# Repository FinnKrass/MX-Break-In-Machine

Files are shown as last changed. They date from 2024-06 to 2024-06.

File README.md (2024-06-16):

# MX Style Switch Break In Machine

Repository is still a work in progress!

A unique take on the switch break in machine intended to streamline the process and maximise outcomes. Useful for those who want to improve the sound and feeling of MX style keyboard switches that come scratchy/inconsistent from the factory.

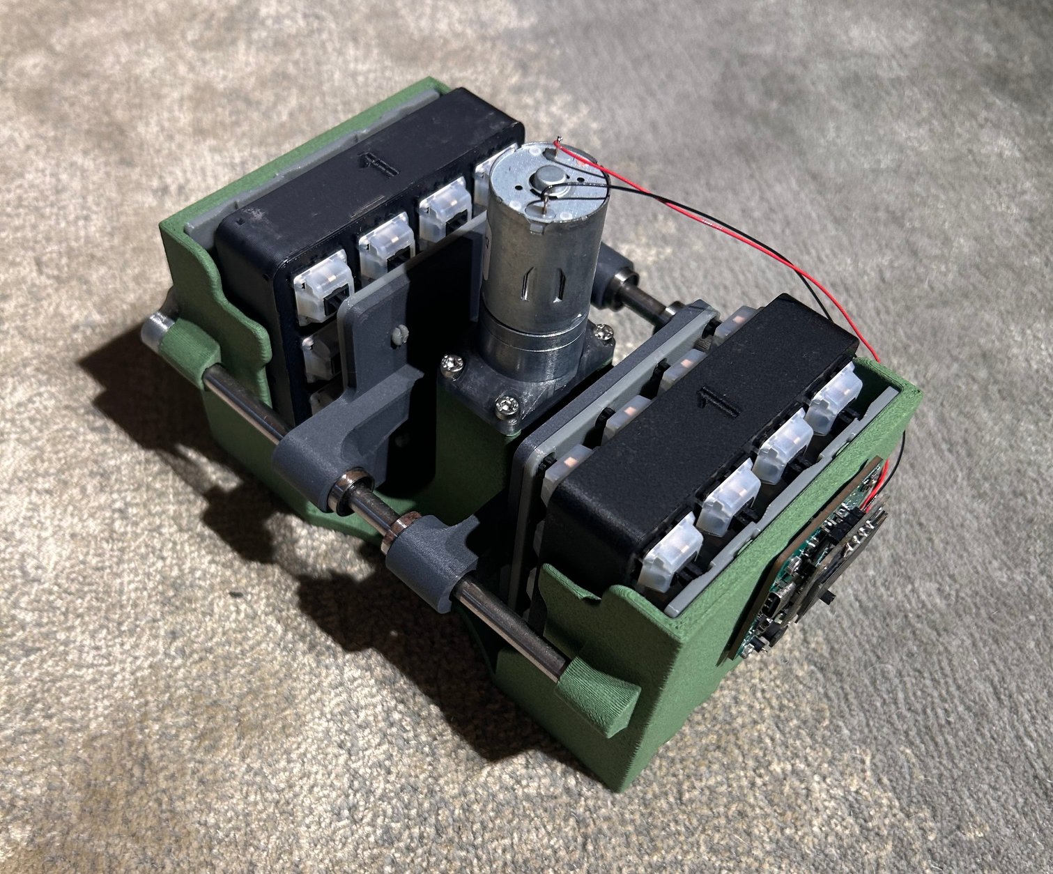
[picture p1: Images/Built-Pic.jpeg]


**Table of Contents:**

- [Main README](#mx-style-switch-break-in-machine)
  
  - [Background](#background)
  
  - [Features](#features)
  
  - [To Do](#to-do)
  
  - [References & Thanks](#references--thanks)

- [Bill of Materials - Hardware](https://github.com/FinnKrass/MX-Break-In-Machine/blob/main/BoM/Bill-of-Materials-(Hardware).md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)
  
  - [Hardware](https://github.com/FinnKrass/MX-Break-In-Machine/blob/main/BoM/Bill-of-Materials-(Hardware).md#hardware)
  
  - [Fasteners](https://github.com/FinnKrass/MX-Break-In-Machine/blob/main/BoM/Bill-of-Materials-(Hardware).md#fasteners)

- [Making Your Own](https://github.com/FinnKrass/MX-Break-In-Machine/blob/main/Documentation/Making-Your-Own.md#making-your-own)
  
  - [Printing](https://github.com/FinnKrass/MX-Break-In-Machine/blob/main/Documentation/Making-Your-Own.md#printing)
    
    - [Print BoM](https://github.com/FinnKrass/MX-Break-In-Machine/blob/main/Documentation/Making-Your-Own.md#print-bom)
  
  - [Additional Hardware](https://github.com/FinnKrass/MX-Break-In-Machine/blob/main/Documentation/Making-Your-Own.md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)
    
    - [Fasteners](https://github.com/FinnKrass/MX-Break-In-Machine/blob/main/Documentation/Making-Your-Own.md#fasteners)
  
  - [Assembly](https://github.com/FinnKrass/MX-Break-In-Machine/blob/main/Documentation/Making-Your-Own.md#assembly)
    
    - [Tools Needed](https://github.com/FinnKrass/MX-Break-In-Machine/blob/main/Documentation/Making-Your-Own.md#tools-needed)
    
    - [Prepare Motor & Limit Switch](https://github.com/FinnKrass/MX-Break-In-Machine/blob/main/Documentation/Making-Your-Own.md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)
    
    - [Prepare Motor Assembly](https://github.com/FinnKrass/MX-Break-In-Machine/blob/main/Documentation/Making-Your-Own.md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)
    
    - [Prepare the Pistons](https://github.com/FinnKrass/MX-Break-In-Machine/blob/main/Documentation/Making-Your-Own.md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)
    
    - [Install the Pistons](https://github.com/FinnKrass/MX-Break-In-Machine/blob/main/Documentation/Making-Your-Own.md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)
    
    - [Install the Motor Assembly](https://github.com/FinnKrass/MX-Break-In-Machine/blob/main/Documentation/Making-Your-Own.md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)
    
    - [Install the PCB](https://github.com/FinnKrass/MX-Break-In-Machine/blob/main/Documentation/Making-Your-Own.md#install-the-pcb)
  
  - [Testing & Notes](https://github.com/FinnKrass/MX-Break-In-Machine/blob/main/Documentation/Making-Your-Own.md#testing--notes)

- [Making the PCB](https://github.com/FinnKrass/MX-Break-In-Machine/blob/main/Documentation/Making-The-PCB.md)
  
  - [Notes](https://github.com/FinnKrass/MX-Break-In-Machine/blob/main/Documentation/Making-The-PCB.md#notes)
  
  - [To Do](https://github.com/FinnKrass/MX-Break-In-Machine/blob/main/Documentation/Making-The-PCB.md#to-do)
  
  - [Ordering from JLCPCB](https://github.com/FinnKrass/MX-Break-In-Machine/blob/main/Documentation/Making-The-PCB.md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)

## Background

This project started when I first fell in love with Cherry MX Black's. I wanted a way to break in the switches for all of my builds, but had absolutely no understanding of electronics and CAD at the time, so took it upon myself to learn how to use Fusion360 and eventually design a circuit. Once the design had come together, I started selling broken in switches with a fleet of these machines running around the clock, which helped me vet the design and iron out any problems as well as optimize certain things to make the labor involved with operating and maintaining the machines easier. I worked on this project on and off over about a year and was planning to sell the machines themselves once they were in a state I was proud of, but some life events got in the way, so I've decided to work back and open source it for others to enjoy as much as I have.

## Features

The machine is quite rugged, I've had customers request their switches broken in for 2.5 million + actuations and the machines have handled that no problem. For good measure, I give them 1 hour break every 12 hours, and have had machines comfortably surpass total lifetime actuations of 75 million. This isn't guaranteed of course, it depends on a plethora of variables, including materials used to print, print profiles, the motor manufacturer, bearing quality etc. Regardless, here is a list of features:

- Linear bearings (inspired by Feng Studio's machine)
  
  - Eliminate plastic on plastic friction
  - Ensure the pistons remain aligned, applying even force on all switches

- Full capacity (64 switches) off centre operation.

- Noise reducing plates
  
  - The biggest issue I had with the machines was the noise. To fix that, rear plates were integrated into the design that would be printed in a flexible material (95A TPU) to dampen the noise produced by the switches colliding with the back walls and pistons.
  - An off centre version of this was introduced later on. There are two models for this; one which attaches to the piston, and one which rests against the back wall. The intention is to operate in off centre at all times.

- USB Power Delivery compatible controller & power supply.

- 128x64 OLED display for information on progress.

- Actuation counter with programmable profiles to disable/enable the motor after *x* number of actuations. Currently programmed to turn off after 250,000 actuations to ensure an even distribution of off centre actuations on all 4 sides.

- Two speeds can be selected via a switch on the PCB.

- Rugged 24V motor, capable 564 actuations/minute. (Faster is not recommended)

- Non-volatile flash memory, will recall number of actuations recorded in the event of power loss.

Here are a few video's showing off the operation. [Video A](https://youtu.be/W0hglbHXOGw), [Video B](https://youtu.be/-IIjR5GEPkg).

Some older video's of their operation can be found [here](https://youtube.com/shorts/SL5bj8C431c) and [here](https://youtube.com/shorts/yf9J68zrslU).

## To-Do

- [ ] Finalise documentation
  
  - [ ] User guide and tips on operating the machine
  
  - [ ] General clean up, more coherent structure.

- [ ] Acceptable print tolerance specifications

- [x] Piston bearing socket tolerance calibration print

- [ ] PCB BoM optimisations (more details in PCB doc)

- [ ] PCB BoM sheet for mouser to automate adding to cart (should be done very soon)

## References & Thanks

The individual who helped me most requested not to be named, but a deep thank you goes out to them for the help they have provided me and continue to provide to the community. Their help is the reason I became more interested in the intricacies of electronics, and that passion has continued far beyond this project now. 

[Kee Keen's open source break in machine](https://github.com/keekeen/MX-Switch-Break-In-Machine/tree/main) helped me greatly in the beginning, definitely check it out if you're interested in the roots of this project!

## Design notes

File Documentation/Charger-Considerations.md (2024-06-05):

## Powering Your Machine

Though the machine is capable of being powered from a standard 5V wall wart/charger, I advise against it for reasons discussed in this document. A charger such as [this](https://www.amazon.com.au/HEBA-Charger-Adapter-Delivery-certified/dp/B096WF4SF2), rated for 20W or greater is more than ample. 

### Reasons for Using USB-PD

Due to the design of the machine, the motor has to exert a *lot* of force when it first starts compared to when it's in operation. This results in a small (~30mA) initial current draw while the RP2040 wakes up, followed by an immediate spike as the boost converter is enabled and the motor receives power. Many low powered / cheap wall wart chargers don't handle this well, causing the motor to stall and controller to lose power. This presents itself in the form of the motor 'pulsating' as it attempts to start, getting caught in that cycle. 

There are two strong advantages to using USB Power Delivery:

- PD capable chargers can supply more power out of the gate, giving the machine more room to breath during the start up process. 

- Boosting 5V to 24V is relatively inefficient in both conversion and conversion losses. Using PD to provide 9V means the switching duty cycle is at a more comfortable level and the range of current consumption is smaller and thus more manageable by the charger.
  
  - USB-PD chargers are also more capable of dealing with dynamic loads such as this.

Though the Power Delivery standard allows for much more power than we utilize, including up to 24V which could directly power the motor, 9V has been selected in order to keep the simple (and low cost) LDO regulator used for supplying 3.3V to the micro-controller. Additionally, using a boost converter allows us to set the speed of the motor via a simple switch which selects between two resistors in the boost converter's feedback network. The boost converter outputs 18V when the switch is set to *75%*, and 24V when set to *100%*.

To **visualize** this, I've compared the *input* current and output voltages for 5V and 9V input. This was just a quick test performed to help explain the reasoning behind the decision to use USB-PD. The sampling rate of my power supply is painfully slow and misses some of the more insightful behaviour.

#### 5V Input

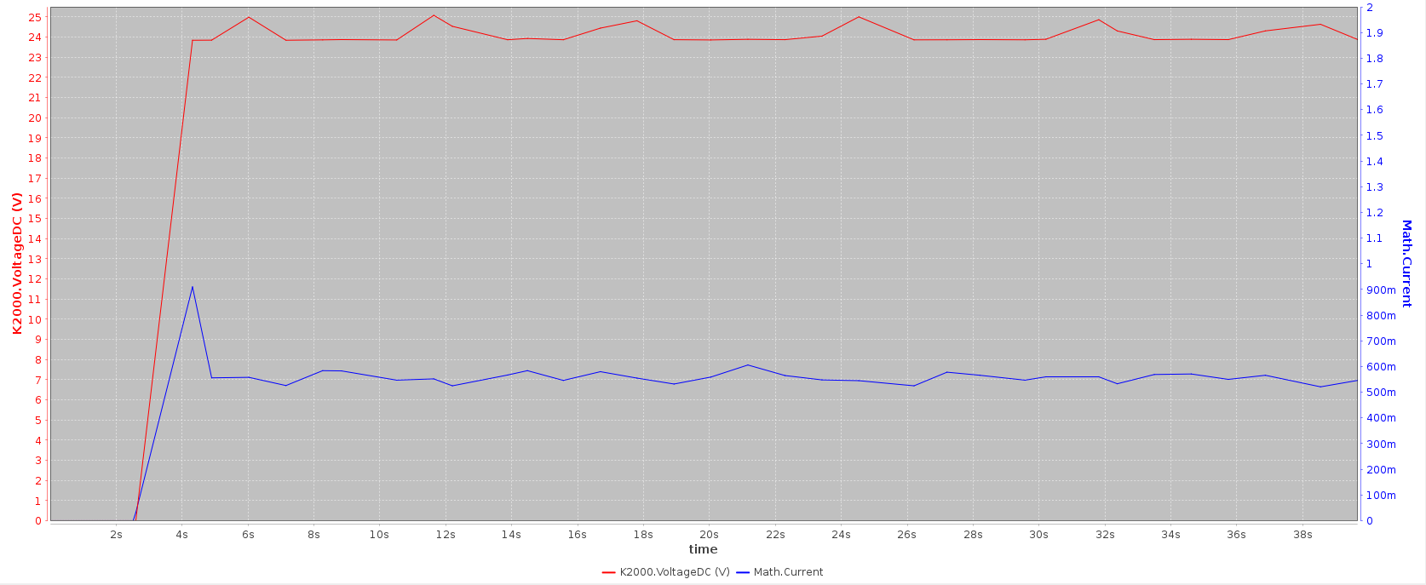
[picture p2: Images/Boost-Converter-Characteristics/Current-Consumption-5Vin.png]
5Vin


#### 9V Input

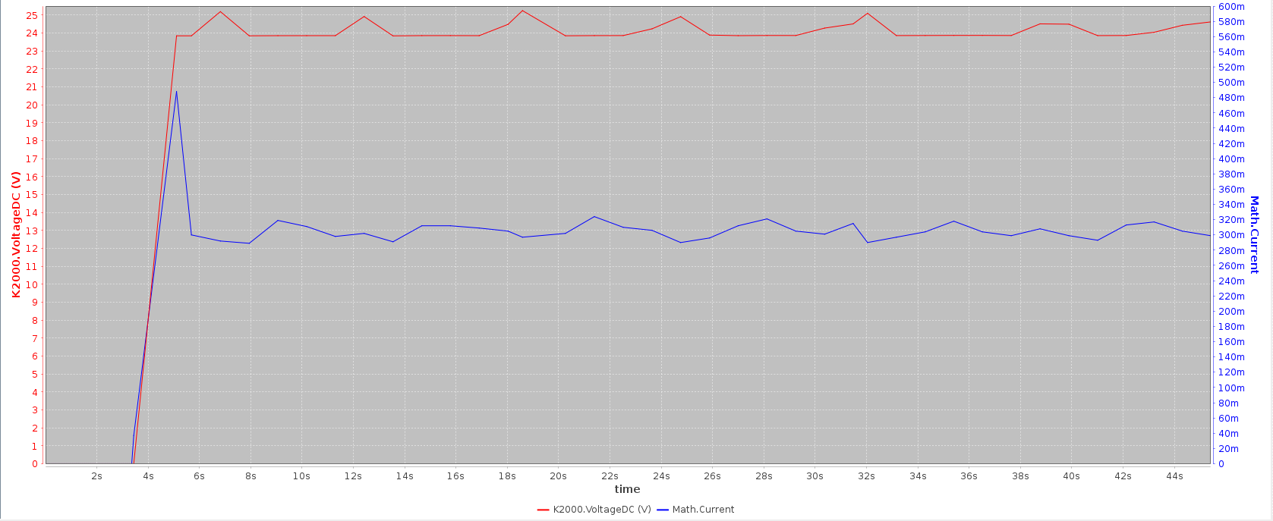
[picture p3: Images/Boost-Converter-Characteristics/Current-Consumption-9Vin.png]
9V Input


#### Current Limited Stall

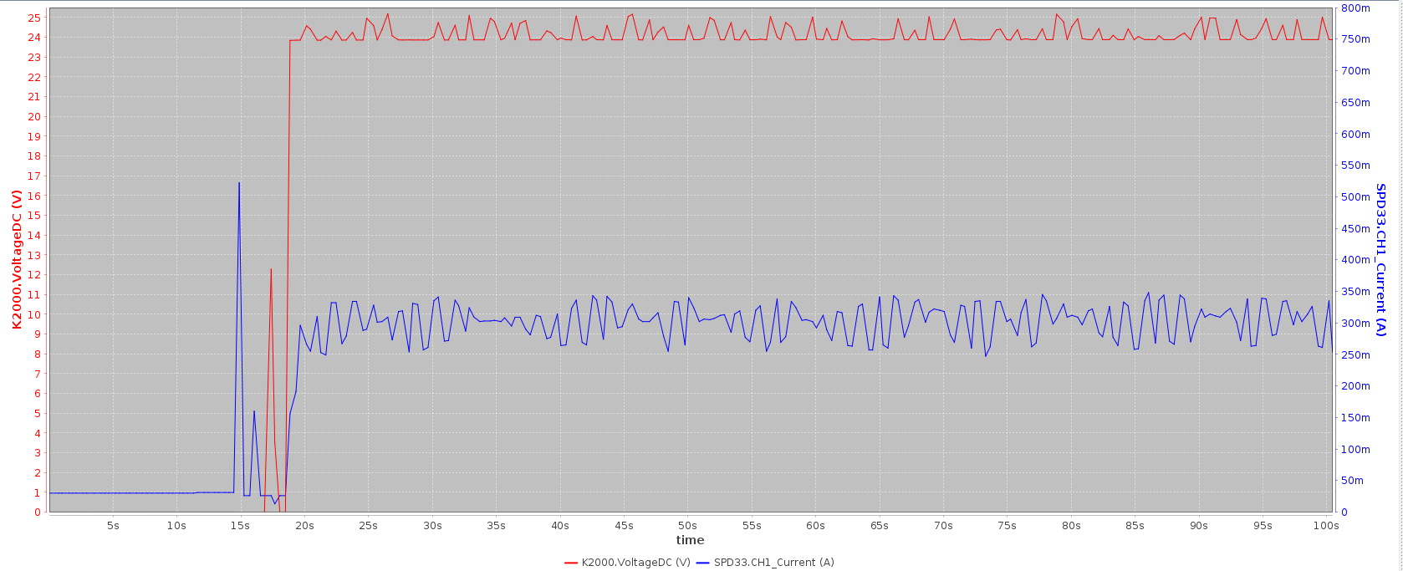
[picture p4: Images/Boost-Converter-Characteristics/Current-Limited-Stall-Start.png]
Current Limited


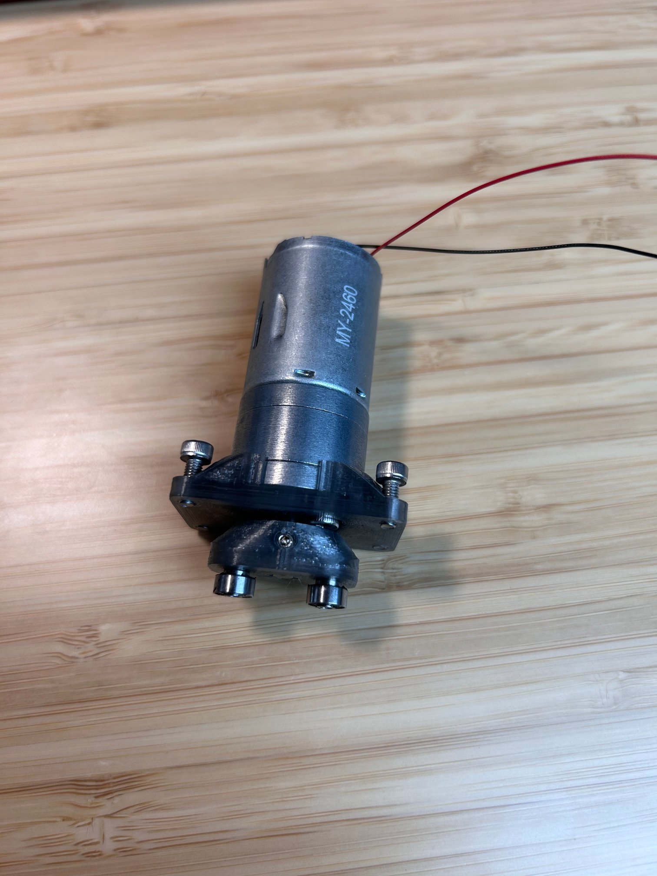
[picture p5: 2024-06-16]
Images/A_Mounting-Plate-Finished.jpeg

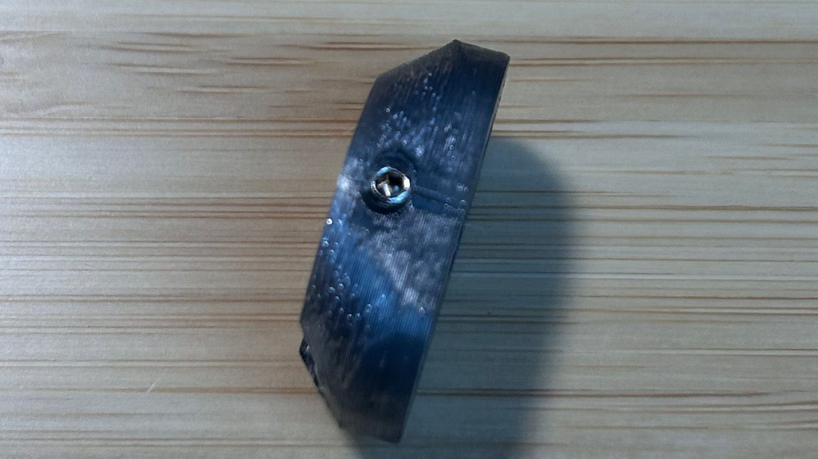
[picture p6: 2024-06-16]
Images/A_Grub-Screw.jpeg

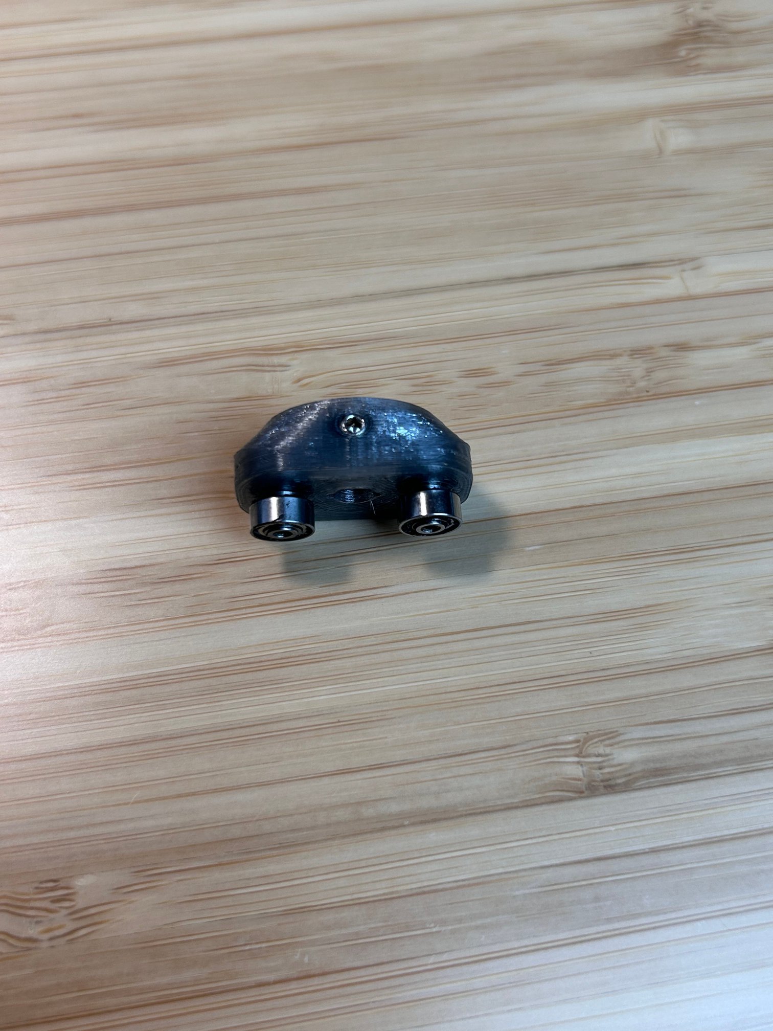
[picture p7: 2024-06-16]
Images/A_Yoke-Bearings.jpeg

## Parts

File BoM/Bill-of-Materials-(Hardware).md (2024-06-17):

## Bill of Materials (Hardware)

There are two documents which outline all components needed in order to make sourcing easier than finding links throughout all of the docs. Links provided here will be for AliExpress (and Taobao where applicable) for the machine itself, and another document is dedicated to components from mouser for the PCB<sup>*</sup>. I wanted to make sourcing as easy as possible, so you should be able to order all of the components you need from just two locations (or one if you're skipping the PCB).

<sub>*The SDB628 and OLED for the PCB are listed here in order to keep all AliExpress links in one place</sub>

### Hardware

AliExpress Choice options have been added where applicable as well, this should speed up shipping and remove some uncertainty. Use these links for speed, non choice options may be cheaper, or just shops that I have experience ordering from. <u>***Please be sure to select the correct options from the links provided.***</u>

| **Name** | **Quantity** | **Description** | **Link** | **Alternative** | AE Choice |
| --- |:---:|:---:|:---:|:---:|:---:|
| JGA25-370 | 1 | 24V 300/282RPM | [link](https://www.aliexpress.com/i/32987942205.html) | [alternative](https://item.taobao.com/item.htm?id=691467377622) | [choice](https://www.aliexpress.com/item/1005006534148010.html) |
| Limit Switch | 1 | Limit Switch | [link](https://www.aliexpress.com/item/1005005708872538.html) | [alternative](https://www.lcsc.com/product-detail/Microswitches_Omron-Electronics_C231399.html) | [choice](https://www.aliexpress.com/item/1005005708872538.html) |
| LM6UU | 4 | Linear Bearing | [link](https://www.aliexpress.com/item/1005004774546723.html) | | [choice](https://www.aliexpress.com/item/4000909626059.html) |
| Yoke Bearing | 2 | C1L6M3 or 3C1L6M3 | [link](https://www.aliexpress.com/item/1005005223529401.html) | [alternative](https://item.taobao.com/item.htm?id=672727759613) | [choice](https://www.aliexpress.com/item/1005002584715570.html) |
| Smooth Rod | 2 | 6 mm | [link](https://www.aliexpress.com/item/1005006293171727.html) | | [choice](https://www.aliexpress.com/item/1005001380920260.html) |

### Fasteners

M3 and M2 kits can be found [here](https://www.aliexpress.com/item/1005005999729125.html) if you don't have any on hand, many of these screws are common in keyboards so some may already own kits like these. The M3x6 grub screw can be found [here](https://www.aliexpress.com/item/1005003125436106.html). 

| Size  | Quantity | Type |
|:----- |:---:|:---:|
| M2x4  | 3 | Hex Socket |
| M2x10 | 2 | Hex Socket |
| M3x5  | 2 | Hex Socket |
| M3x6  | 2 | Hex Socket |
| M3x6  | 1 | Grub Screw |
| M3x8  | 4 | Hex Socket |
| M3 | 3 | Hex Nut |

### PCB

| Name | Quantity | Link | Alternative |
| --- |:---:|:---:|:---:|
| SDB628 | 10 (min order q) | [link](https://www.aliexpress.com/item/1005001682782080.html) | [alternative](https://www.aliexpress.com/item/32868057947.html) |
| OLED 128x64 (0.96") | 1 | [link](https://www.aliexpress.com/item/1005004993682117.html) | [alternative](https://www.aliexpress.com/item/32638662748.html) |

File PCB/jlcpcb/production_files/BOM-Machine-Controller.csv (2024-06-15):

Comment | Designator | Footprint | LCSC
1uF | C2 | C_0805_2012Metric | C116352
SS34B | D5 | D_SMB | C13762
22uF | C1,C20,C21,C22,C3,C6 | C_0805_2012Metric | C15850
USB_C_Receptacle_USB2.0 | J6 | USB_C_Receptacle_HRO_TYPE-C-31-M-12 | C165948
12MHz | Y2 | OSC_CSTNE12M0G520000R0 | C1857787
RP2040 | U5 | RP2040-QFN-56 | C2040
1N4148 | D3,D4 | D_SOD-323F | C2128
SSM3J340R | Q1 | SOT-23-3F | C2592
0.1uF | C10,C11,C12,C13,C14,C15,C16,C18,C19,C24,C8,C9 | C_0402_1005Metric | C2649532
W25Q16JVUXIQ | U2 | USON-8_2x3x0.6mm | C2843335
10m | R19 | R_0603_1608Metric | C2848992
27R | R14,R15 | R_0603_1608Metric | C2907136
PUSB3FS4Z | D6 | DFN2510A-10 | C2923351
1k | R5,R8 | R_0402_1005Metric | C2991282
22uH | L1 | TDK-VLS5045-5x5.3x4.5 | C307873
BTN_UR | SW3,SW4 | SW_SPST_TL3342 | C318884
29K | R1 | R_0805_2012Metric | C322401
3K8 | R18 | R_0603_1608Metric | C325680
22uF | C4,C5 | C_0603_1608Metric | C386015
39K | R7 | R_0805_2012Metric | C413307
78171-0002 | J4,J7 | Molex_Pico-EZmate_78171-0002_1x02 | C505023
1uF | C17,C23,C25,C26,C7 | C_0603_1608Metric | C5137572
BZX84C22-7-F | D1 | SOT-23-3 | C516601
10k | R10,R11,R12,R13,R17,R2,R20,R21,R3,R4,R6,R9 | R_0603_1608Metric | C5355234
SDB628 | U1 | SOT-23-6 | C77805
100R | R16 | R_0603_1608Metric | C844513

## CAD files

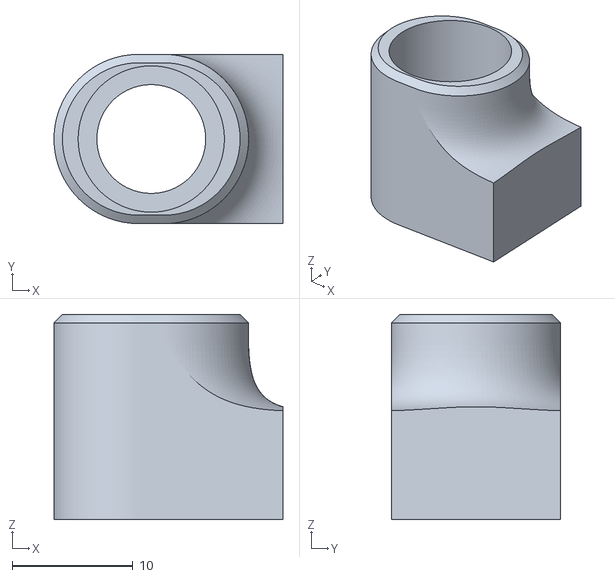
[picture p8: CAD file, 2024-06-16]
3D Models/Piston-Calibration.stl
19.0 x 14.0 x 17.0

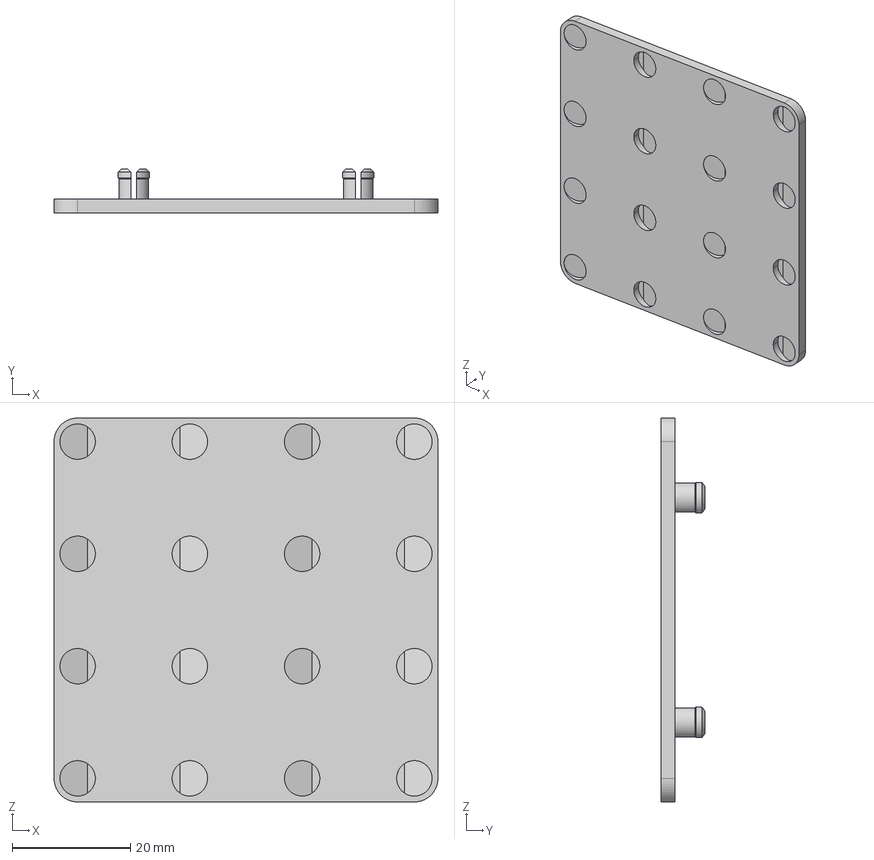
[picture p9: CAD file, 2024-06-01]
3D Models/Off-Centre_Piston-Sleeve.step
65.0 x 7.42 x 65.0 mm

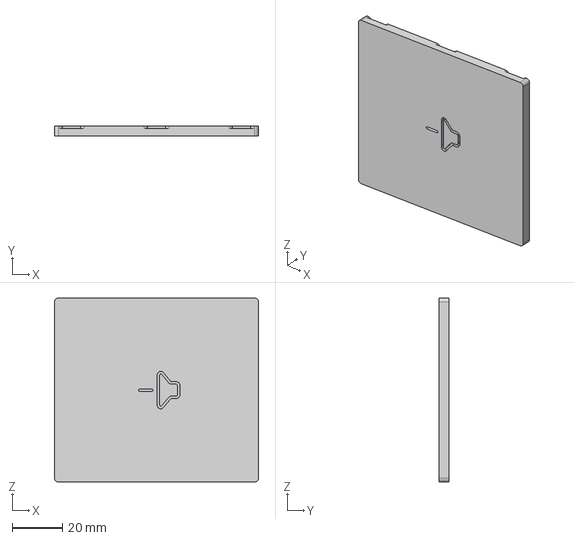
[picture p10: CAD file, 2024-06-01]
3D Models/Back-Plate.step
81.0 x 4.10 x 73.0 mm

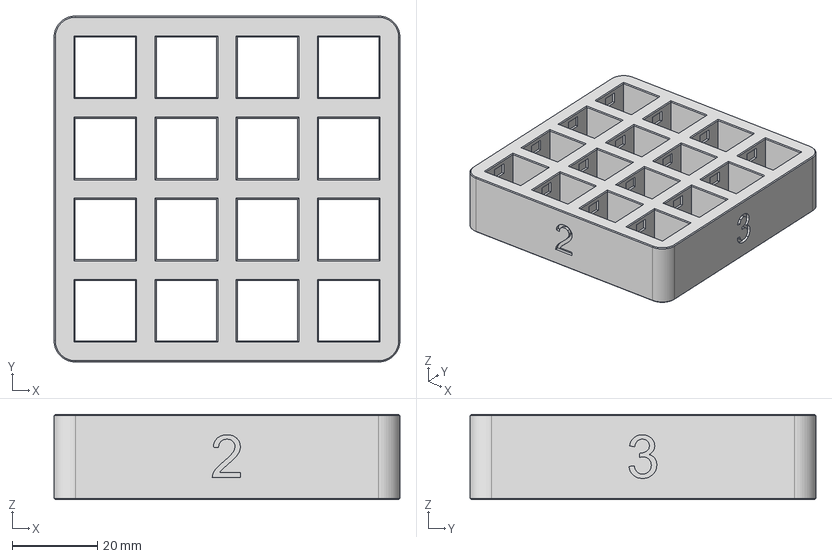
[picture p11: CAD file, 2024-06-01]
3D Models/4x4-Switch-Tray.step
81.0 x 81.0 x 20.0 mm

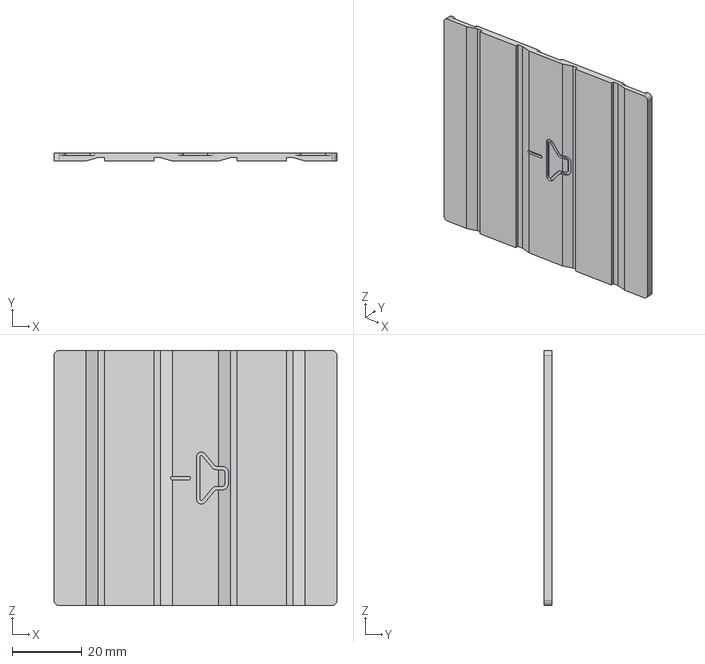
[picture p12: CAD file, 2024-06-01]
3D Models/Off-Centre_Back-Plate.step
81.0 x 2.32 x 73.0 mm

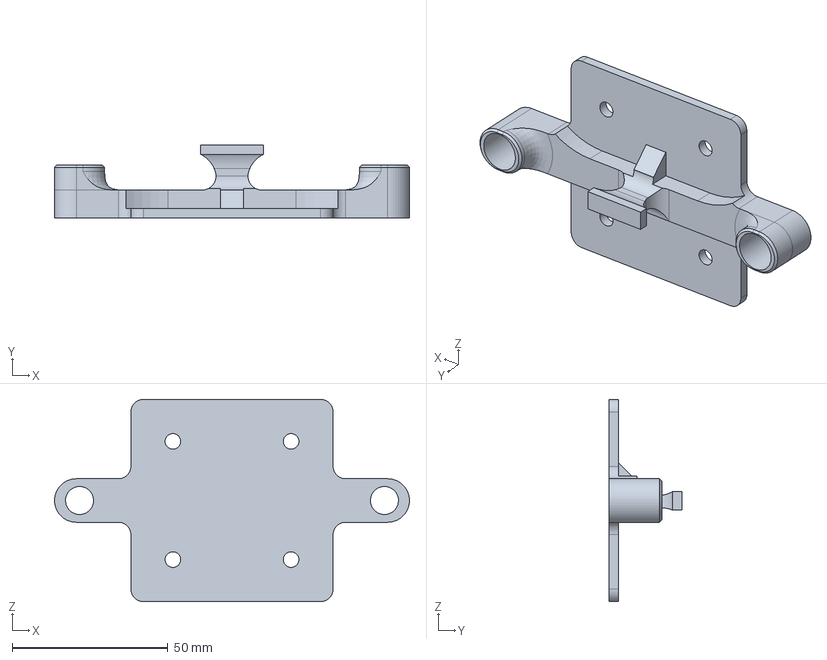
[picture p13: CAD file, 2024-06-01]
3D Models/Piston.step
114.1 x 23.5 x 65.0 mm

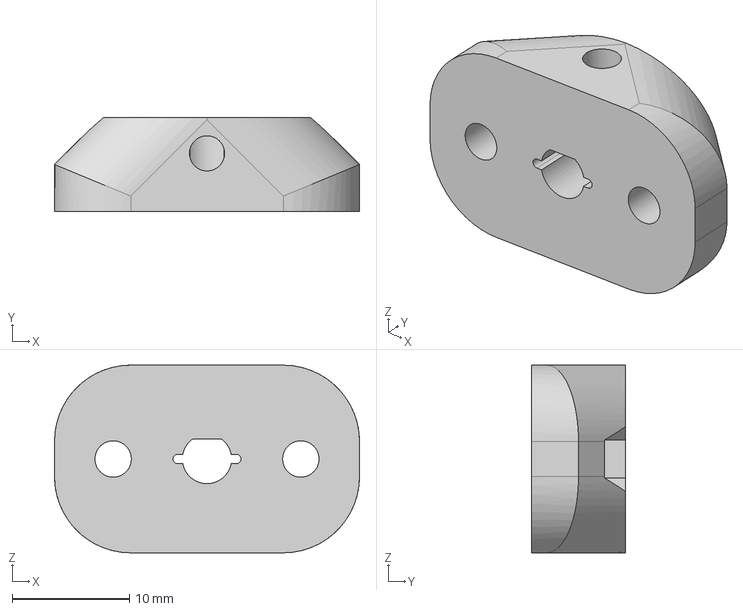
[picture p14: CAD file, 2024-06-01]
3D Models/Motor_Yoke.step
26.0 x 8.00 x 16.0 mm

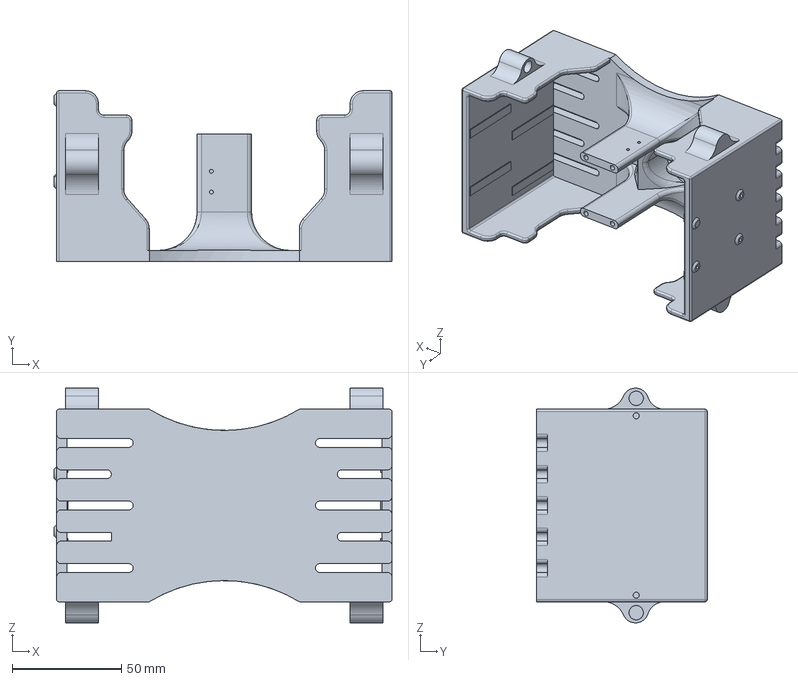
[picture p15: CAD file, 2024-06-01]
3D Models/Machine-Housing-V3.1.step
154.5 x 78.0 x 107.3 mm

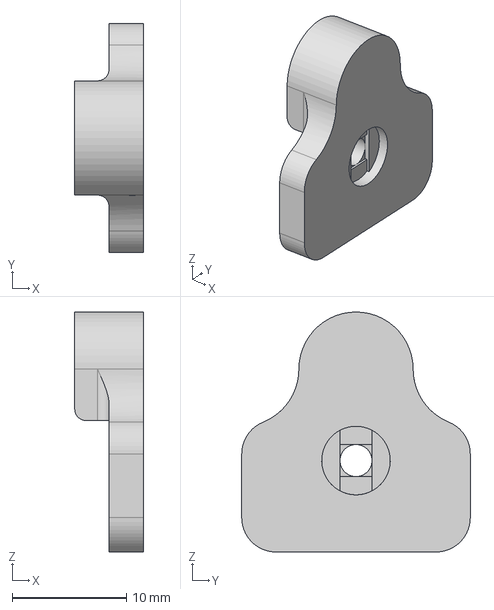
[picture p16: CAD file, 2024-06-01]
3D Models/Rod-Cap.step
6.00 x 20.0 x 21.0 mm

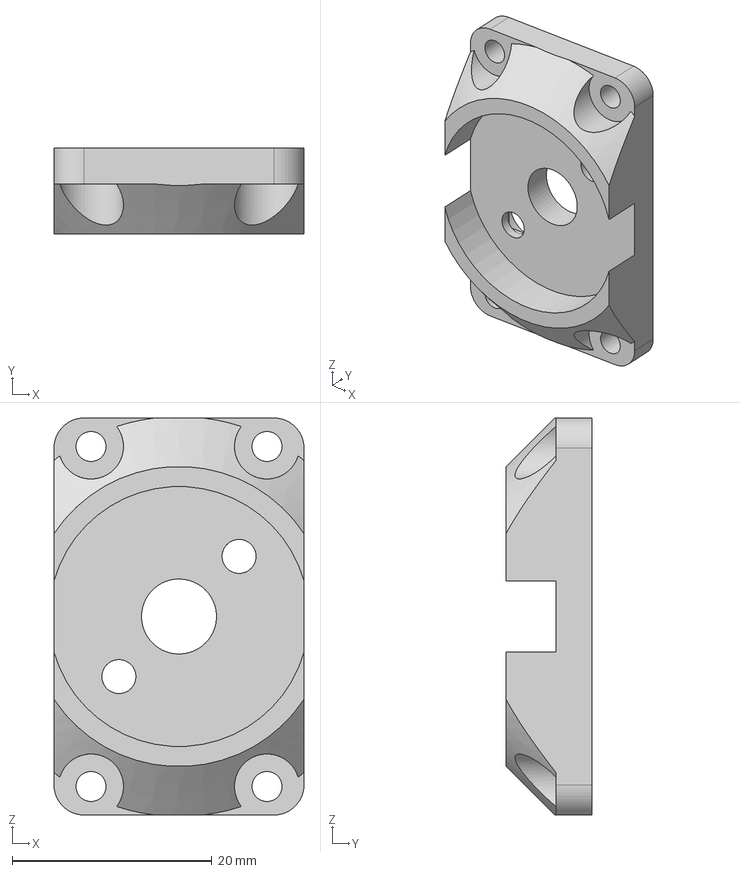
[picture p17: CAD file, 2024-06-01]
3D Models/Motor_Mounting-Plate.step
25.0 x 8.60 x 39.7 mm

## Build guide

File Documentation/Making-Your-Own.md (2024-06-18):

## Making Your Own

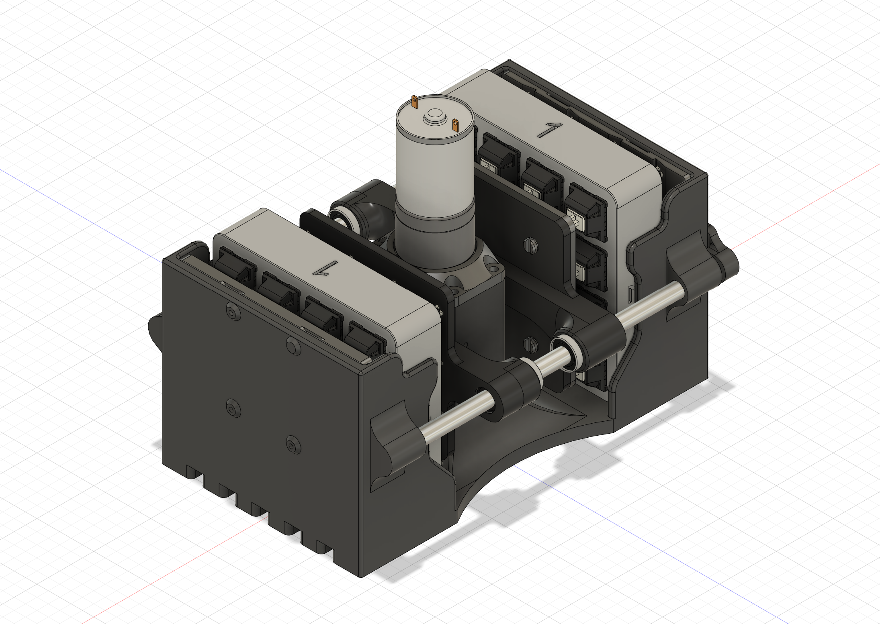
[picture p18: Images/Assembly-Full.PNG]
Header Img


**NOTE:**

It's suggested to read through the repo in whole before choosing to build one, there will be notes for each section which will include vital information. If you find any issues in the design or gaps in the documentation, feel free to open a github issue and the problem will be addressed.

The PCB/Controller is not necessary if it's too much of a hassle to get manufactured and assembled. The assembled PCB's may be sold at some point if there's interest, but otherwise you just need a 24V power source (or get the 12V motor and a 12V power source).

Another thing worth mentioning is that a lot of the design decisions were made for repeatability, convenience, and cost saving. This is to say, there are likely areas which can be improved for an end user. 

**Cloning the repository**

Open terminal in your folder of choice:

`git clone https://github.com/FinnKrass/MX-Break-In-Machine.git`

then:

`cd MX-Break-In-Machine`

and lastly:

`git submodule init`

### Printing

It's a good idea to make the prints rugged, so for each item in the print BoM there will be a corresponding *suggested* material. These can be changed, but I can't guarantee the longevity if substituted for a weaker material. I've only tested the off centre plates in TPU, so I can't guarantee functionality if printed in standard materials. It's important that you have your TPU print profiles dialled in for the off centre plates, there are a handful of bridges and some steep overhangs. Where applicable, alternative materials are listed. 

When selecting the print settings, make sure you use ~6 perimeters and 25% (gyroid) infill. For some parts this strength isn't critical, so feel free to make changes at your own liberty. I've also selected the primary material choices to be attainable at a reasonable price and printable by beginners, but if any Nylon filaments are listed as an alternative and you have some on hand, then use that!  The last thing to note is that supports are not needed for any part, there's a few short bridges and mild overhangs, but all printers should be able to handle that. Screw bores that are on the bottom surface are modelled with sequential bridging, these print cleanly without supports but your slicer may automatically add them without you realising *so make sure to disable automatic supports*.

#### Print BoM

| Name | Quantity | Material | Optional | Alternative |
|:--- |:---:|:---:|:---:|:---:|
| Switch Tray | 2 | PLA | NO | PETG/PLA-CF/ABS |
| Back Plate | 2 | TPU | NO | PLA/PETG/ABS |
| Machine Housing | 1 | PETG-CF  | NO | PETG/PLA-CF/ABS |
| Motor Mounting Plate | 1 | PETG-CF  | NO | PA-CF/PAHT-CF |
| Motor Yoke | 1 | PETG-CF  | NO | PA-CF/PAHT-CF |
| Piston | 2 | PETG-CF  | NO | PLA-CF/ABS |
| Rod Cap | 2 | PLA | NO | PETG/PLA-CF/ABS |
| OC Back Plate | 2 | TPU | YES | N/A |
| OC Piston Sleeve | 2 | TPU | YES | N/A |

OC = Off Centre, PA = Nylon

*NOTE:*

Please keep in mind that print tolerances vary between printers (and even print settings). Each piston requires bearings to be pressure fitted for the linear rails. Print the model "Piston-Calibration" first, if the bearing fits snug then you're good to go, but if it's too tight or too loose then you can tweak it using the X-Y hole compensation setting in your slicer. This can be very sensitive, so adjust in +/- 50 micron steps. When you're happy with the fit on the calibration model, go ahead and print the full model with the appropriate X-Y compensation.

#### Additional Hardware

*Sourcing Notes:* 

There are dedicated documents covering the BoM for the entire project to make sourcing easier. If you're fine purchasing from the AliExpress links provided, you can mostly ignore the following notes as they cover things to look out for when sourcing elsewhere.

The JGA25-370 is easy to find, I've linked product pages I've used but if it's easier to purchase elsewhere then just make sure you buy the correct voltage/speed. The same applies for the linear bearings (LM6UU), though there is a huge difference in quality comparing cheap to expensive. If you get the cheap ones (sub 50c each), buy a handful of extras in case bearings comes out or they're not gliding freely along the rod. The more expensive ones may be worth it if you're going for longevity, if you're in Australia use [these](https://www.makerstore.com.au/product/bear-lm6uu/), and if you can't find any local to yourself then use the links provided in the table below and pick up extras.

For the yoke bearings, the naming scheme is inconsistent across sellers, so purchase based off [dimensions](https://github.com/FinnKrass/MX-Break-In-Machine/blob/main/Images/Yoke-Bearing.png) if the part number doesn't resemble what's listed in the table below. 

For the 6mm smooth rod there are a few ways you can purchase them, one example has been linked. The length required is 145mm +/- 5mm, and you can usually find stores which sell them pre cut to 150mm which works just fine, or if you can only find greater lengths then just cut them down to size. Alternatively some suppliers will let you request a specific length, in which case have them cut to 145mm. No matter how you arrive at the 145mm +/- 5mm, you should check both ends and make sure they're smooth/free of burrs. If the ends aren't smooth there's a chance that the rod will catch on the bearing balls inside the linear bearing, which will break it.

If you choose not to have the PCB and bring your own power source, you can omit the cable harnesses in favour of the correct cable for your power source. The cable linked below is used to connect the limit switch (which counts actuations) and motor to the circuit board.

| Name | Quantity | Optional | Description | Link |
|:--- |:---:|:---:|:---:|:---:|
| JGA25-370 | 1 | NO | 24V 300/282RPM | [link](https://www.aliexpress.com/i/32987942205.html)/[alternative](https://item.taobao.com/item.htm?id=691467377622) |
| SS-01GL2 | 1 | YES | Limit Switch | [link](https://www.lcsc.com/product-detail/Microswitches_Omron-Electronics_C231399.html)/[alternative](https://www.aliexpress.com/item/1005005708872538.html) |
| LM6UU | 4 | NO | Linear Bearing | [link](https://www.aliexpress.com/item/1005004774546723.html) |
| Yoke Bearing  | 2 | NO | C1L6M3 or 3C1L6M3 | [link](https://www.aliexpress.com/item/1005005223529401.html)/[alternative](https://item.taobao.com/item.htm?id=672727759613) |
| Cable Harness | 2 | YES | 36920-0202 | [link](https://au.mouser.com/ProductDetail/Molex/36920-0202) |
| Smooth Rod | 2 | NO | 6 mm | [link](https://www.aliexpress.com/item/1005006293171727.html) |

##### Fasteners

| Size  | Quantity | Type |
|:----- |:---:|:---:|
| M2x4  | 3 | Hex Socket |
| M2x10 | 2 | Hex Socket |
| M3x5  | 2 | Hex Socket |
| M3x6  | 2 | Hex Socket |
| M3x6  | 1 | Grub Screw |
| M3x8  | 4 | Hex Socket |
| M3 | 3 | Hex Nut |

### Assembly

This drawing should be referenced throughout the assembly process. It tells you what screws go where. There are also hyper-links to relevant images scattered throughout the assembly steps in case visual clarification is needed.

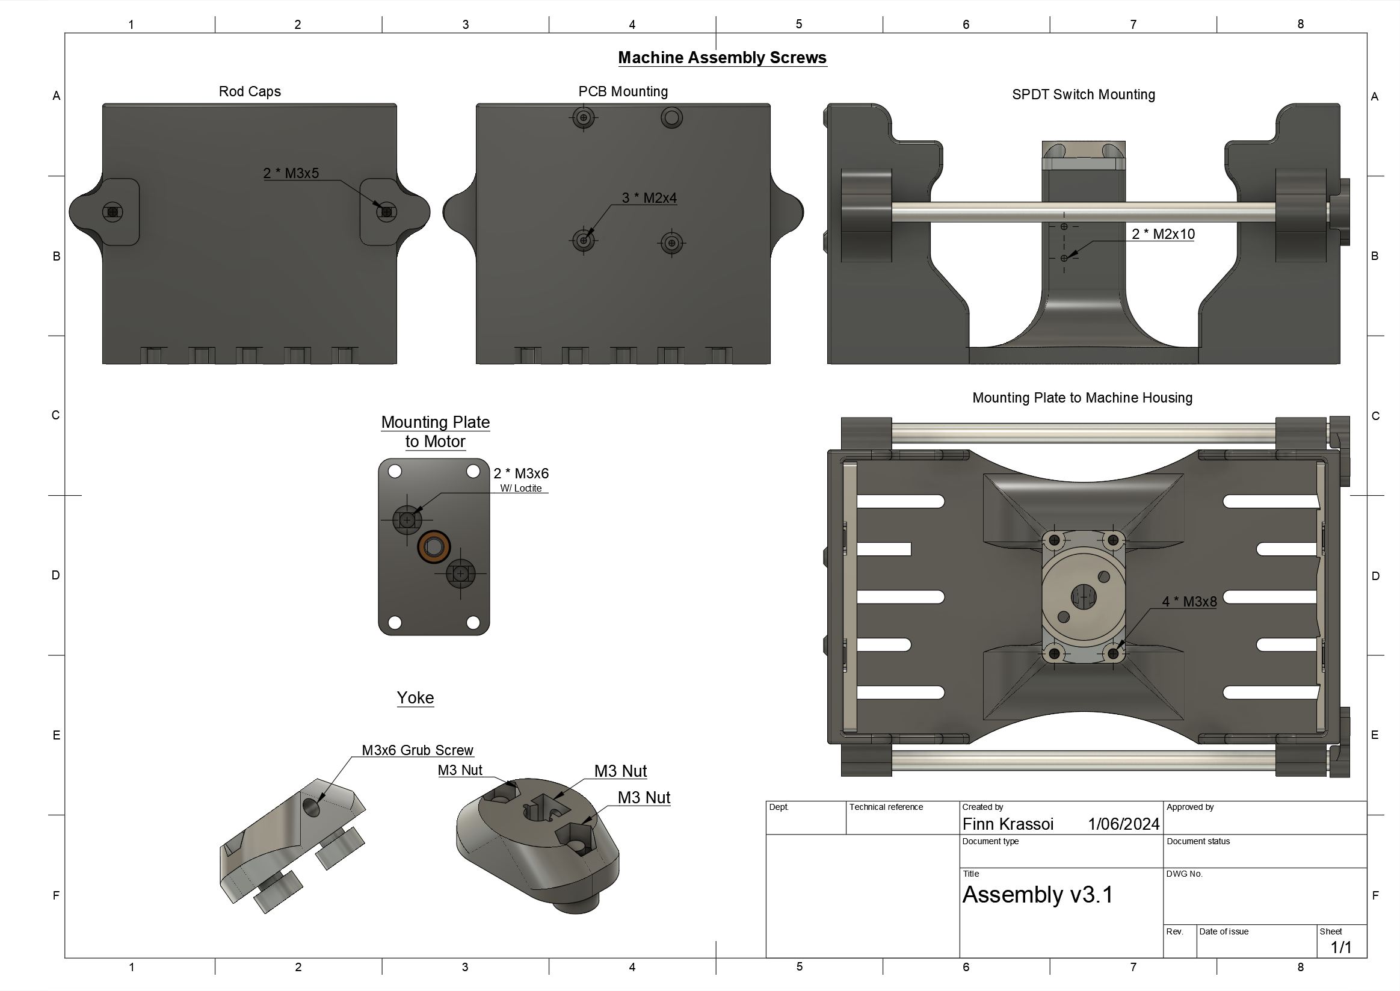
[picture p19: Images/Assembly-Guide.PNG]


#### Tools Needed:

- H1.5 Hex Bit/Key
- H2.5 Hex Bit/Key
- Soldering Iron 
- Hammer (optional)
- Needle Nose Pliers (optional)
- Loctite (optional)

#### Preparing the Motor & Limit Switch

*NOTE:* Limit switch == SPDT switch

A good starting point is soldering the cable harnesses to the limit switch and motor. The orientation of the cable doesn't matter for either part, but the limit switch can be confusing since it has 3 pins. If your limit switch has the pin names de-bossed on it's case, e.g. "NC, NO, C" then the two pins we need are "NO" and "C". If it doesn't have the pin names on the casing, then position the switch on the machine housing as it should be when the unit is fully assembled (or see [here](https://github.com/FinnKrass/MX-Break-In-Machine/blob/main/Images/A_Limit-Switch.jpeg)). The bottom two pins are the ones we're interested in.

You can attach the limit switch to the machine housing now. It attaches using 2 M2x10 screws as shown in the drawing above.

#### Prepare the Motor Assembly

Insert the three M3 hex nuts into the [yoke](https://github.com/FinnKrass/MX-Break-In-Machine/blob/main/Images/Hex-Nuts.jpeg). Depending on your printer tolerances, they may be difficult to get it. If that is the case, use a pair of needle nose pliers to *carefully* clamp each hex nut into plate. Once that's done, locate the hole on the side of the yoke for the M3x6 [grub screw](https://github.com/FinnKrass/MX-Break-In-Machine/blob/main/Images/A_Grub-Screw.jpeg) to go into. Screw in the grub screw using a H1.5 hex bit, don't fully insert it yet, just tighten until the threads engage with the hex nut. After that, you can insert the [yoke bearings](https://github.com/FinnKrass/MX-Break-In-Machine/blob/main/Images/A_Yoke-Bearings.jpeg) and tighten them fully. Set the yoke aside for the moment and move to the motor and mounting plate.

Place the motor into the mounting plate, lining up the two screw holes on the motor with the holes in the mounting plate. [Fasten the motor to the plate](https://github.com/FinnKrass/MX-Break-In-Machine/blob/main/Images/A_Mounting-Plate.jpeg) using two M3x6 screws, optionally adding a dab of loctite to each screw before tightening. Now you can slide the yoke onto the shaft of the motor, lining up the flat edge of the shaft with the hex nut/grub screw in the yoke. If you can't slide the yoke on, loosen the grub screw a little bit and try again. Then tighten the grub screw, securing the yoke on the shaft (tight enough that you can't full the yoke off, if the hex bit slips then you're more than good). The end product should look like [this](https://github.com/FinnKrass/MX-Break-In-Machine/blob/main/Images/A_Mounting-Plate-Finished.jpeg) / [this](https://github.com/FinnKrass/MX-Break-In-Machine/blob/main/Images/A_Mounting-Plate-Finished-B.jpeg). 

#### Prepare the Pistons

This step is very easy if you've tuned the print profile for the bearings to fit, but can be a bit of a pain otherwise. Since the bearings are press fit, the tolerances of the print are important. 

You just need to press fit the linear bearings (4 x LM6UU's) into the two pistons. The models current dimensions are perfect on my X1 Carbon and I can push them in by hand with a bit of force. If you can only get the bearing in partially by hand, use a hammer to very gently tap it in the rest of the way. Let gravity do the work with the hammer, too much force can break the print. If you find the bearing is too easy to push in, it's best if you go back and tune the print settings a bit more. Even though it may be difficult to pull the bearing back out, over time the plastic will stretch and you'll find the bearing comes out of the piston when in operation. You can add a dab of super-glue if you don't want to waste a print, but I don't recommend this since there may be room for the bearing to not be perfectly aligned.

If you have printed the off centre sleeves, attach them to the pistons now.

#### Install the Pistons

Keep in mind the orientation of the plates. The side with a chamfered slope should be facing the floor of the machine, and the flat edge should be facing upward.

Take one of the two 6 mm smooth rods and insert it into either of the openings just far enough to slide one of the pistons onto it, as shown [here](https://github.com/FinnKrass/MX-Break-In-Machine/blob/main/Images/A_Install-Pistons1.jpeg). After sliding the first piston onto the rod, push the rod through until it's approximately 3/4 of the distance to the socket on the other end. Slide on the second piston, then push the rod all the way into the socket as shown [here](https://github.com/FinnKrass/MX-Break-In-Machine/blob/main/Images/A_Install-Pistons1.jpeg). Install the second rod, lifting each piston and guiding it onto the rod, then install the two rod caps to secure them in place. The final result should look like [this](https://github.com/FinnKrass/MX-Break-In-Machine/blob/main/Images/A_Install-Pistons1.jpeg).

At this stage, test the pistons movement by sliding each back and forth. Push them from the centre of the plate, if there's uneven pressure the bearings won't move freely. If the pistons move back and forth with very little resistance, you're good to go! If they feel stiff or bumpy, check each bearing is sitting flat in the piston. If not, remove the piston and *very gently* tap the bearing with a hammer until it is sitting flat in the socket. 

#### Install the Motor Assembly

Twist the yoke so that it's [resting flat](https://github.com/FinnKrass/MX-Break-In-Machine/blob/main/Images/A_Mounting-Plate-Finished-B.jpeg). It's easiest if you insert the 4 M3x8 screws into the mounting plate before attempting to attach it. Screw them just far enough that the end of the screw is flush with the bottom of the mounting plate, then place the [motor assembly onto the posts](https://github.com/FinnKrass/MX-Break-In-Machine/blob/main/Images/A_Install-Motor-Assembly.jpeg) before tightening it down. The screws will cut their own threads so don't worry if it feels difficult, just make sure that each screw is completely tightened down.

#### Install the PCB

*NOTE:* When connecting the switch and motor cables, make sure there are no MX switches in the machine and that the limit switch is completely open. Power the machine up once to confirm that the motor is spinning before inserting the switch trays. When switch trays are inserted, the limit switch will be held closed whilst the machine is off, meaning the boost converter output will be shorted to ground in the event that the cables are installed in the wrong positions.

Secure the PCB to the machine using 3 M2x4 screws. Connect the motor cable to the bottom right connector on the PCB labelled "MOTOR". Connect the limit switch cable to the connector labelled "COUNT", located directly above that of the motor.

### Testing & Notes

Your first time powering up the machine should be without any switches loaded. Supply power via a USB-C cable from a charger of your choice (chargers are discussed in the main readme). On first power up, the motor will remain off until the user holds down the top right button for 1 or more seconds. Hold the top right button for 1 second and then release it, the motor should start spinning. Press the limit switch down and confirm that the actuation counter incremented by 1. Pressing the top right button for less than 1 second will reset the count to 0. 

Once you have confirmed the machine is working, it's time to load it up with some switches and enjoy! For instructions and notes on general usage, please refer to the documentation on operation.

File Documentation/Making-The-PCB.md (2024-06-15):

## Building or Manufacturing the PCB

In terms of keeping track and managing batches of switches, the PCB has been an invaluable part of this project. Though it isn't necessary, it is incredibly helpful if you're looking for even results throughout a large batch. The firmware and final design are still a work in progress, lately it has taken a back seat as I've been working on other (volt-nut related) projects, but as I learn new things I come back and improve on different areas. 

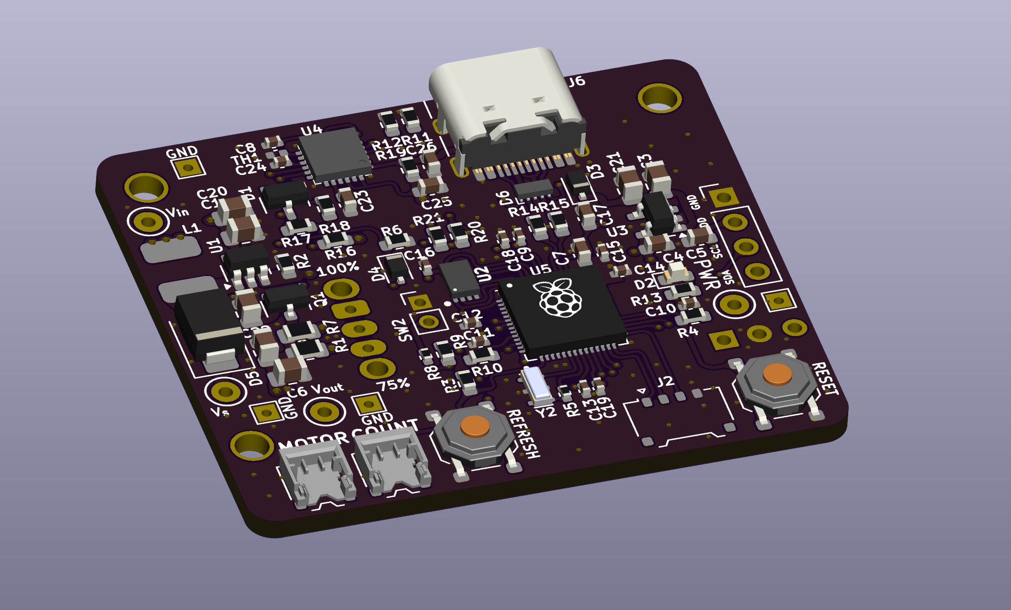
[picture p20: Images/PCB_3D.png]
PCB 3D Render


**Who is this page for?** 

This page is primarily for those unacquainted with the process of ordering from JLCPCB. The ordering process is quite standard so those who understand it may skip the majority of this page, however I do suggest reading the notes section below as it contains some information on sourcing components for the BoM which are applicable to those assembling themselves AND through JLCPCB.

#### Notes:

The PCB was *mostly* designed around Mouser's inventory, so despite my efforts there are certain components that simply aren't available for JLCPCB assembly. Comparing the JLCPCB BoM (/PCB/jlcpcb/production_files/BOM-Boost-Converter.csv) to the iBoM (/bom/ibom.html), you'll notice that some component values have been changed. This is completely fine and should have no impact on operation. The closest value was chosen for components where values were critical, and for less critical components, values were chosen based on availability. 

Alternative parts have been listed where applicable, though currently the AP33772 is not available for JLCPCB assembly and will need to be sourced elsewhere. This chip can be omitted at the expense of USB-PD, not ideal but you can just use a beefy 5V charger and be fine. The biggest hurdle here is soldering its QFN package, which may be difficult/impossible depending on tools and skill. I am looking at changing this to a more convenient PD controller, but for now you can either bring your own or omit it entirely. Another component that needs to be sourced elsewhere is the AP7370-33W5 LDO, responsible for providing 3.3V to the RP200. This component is much easier to solder by hand, and is available from mouser along with the AP33772.

The SSD1306 display needs to be sourced and soldered by the user. I have ordered [these](https://www.aliexpress.com/item/32638662748.html) in bulk since they're so cheap, but they can be readily found from local hobby stores in most countries. It's important that you ensure the pinout is the same as the one linked, pin 1 being "GND" and pin 4 being "SDA", as there are some on the marked which have GND and VCC inverted. If sourcing this configuration is an issue in your country, it's easy enough to swap the pins in the design files, however I suggest ordering the correct configuration through AliExpress/TaoBao since they are significantly cheaper.

If you choose to source all of the components and assemble it yourself, the SDB628 (boost converter) can be had for around 20 cents each in low quantity from either AliExpress, Taobao or LCSC. Occasionally it can be sourced elsewhere, and there are several "drop in replacements" which seem to be the same silicon with a different label. One of these has been listed as an alternative, I haven't listed others as I have not personally verified they are the same (at least in function). Of course, this isn't ideal and I may change to an IC which can be sourced from mouser/digikey, but the price to performance of this chip is amazing and they're great to have on hand for other projects, so pick up some spares while you're at it!

### To Do:

- Tidy up the firmware to make it a more user friendly / smooth experience (I was still very new to programming & completely new to embedded programming, it ***needs*** to be cleaned up or re-written entirely when I have time).

- BoM optimisations for JLCPCB assembly.
  
  - Possibly replace the SDB628 with a more widely (mouser, digikey, etc.) available chip.

- Change to a more readily available USB-PD controller.
  
  - Looking at resistor configurable options.

### Ordering from JLCPCB

#### The PCB

Production files for JLCPCB can be found in the '/jlcpcb/production_files' directory. Navigate to the JLCPCB home page [jlcpcb.com](jlcpcb.com) and create / log into your account. Drag the zip file 'GERBER-Machine-Controller.zip' into the 'Add gerber file' drop box on the home page, or upload the file after clicking 'Instant Quote'. Once the upload has finished, you should be taken to the order page which will let you specify how the PCB is manufactured. All options can be left as default except for 'Remove Order Number' which should be set to 'Specify a location'. If you choose to order through another fab service, make sure you replace the silkscreen on the PCB (under the USB-C port) to correspond with that of your fab house. The order number will be hidden once the board is assembled, so don't feel you need to pay extra to have it removed.  Optionally select ENIG for the surface finish if you're happy to splurge a bit, I like doing this since it's easier to work with when assembling and the pads can take a bit more heat, but HASL is absolutely fine as well.

If you're assembling the PCB yourself, don't forget to order a stencil! I've done this more times than I care to admit, and hand soldering everything takes hours. You can save to cart and order now.

#### JLCPCB Assembly

At the bottom of the configuration page you'll find an option "PCB Assembly" which should be ticked. Initially the design was double sided, but for the sake of convenience and saving an extra set-up to assemble 5 parts, everything has been moved to the front layer. 

- For reference, one sided assembly is roughly 17 AUD and the price for both sides assembled was roughly 100 AUD, this is *before* component sourcing and fees. 

Tick the "Confirm Parts Placement" if you want to play on the safe side, sometimes JLCPCB's positioning tool which we come across later can show components rotated incorrectly or mirrored entirely (this is just a bug in their API, it happens no matter how I export production files/CPL file). Usually they fix this even if the option isn't ticked, but I can't guarantee that (logically they should fix any issues with placement since PNP would be impossible otherwise, I just don't want to promise something that I have no involvement in). Click the blue confirm button to proceed. 

You should have the options to upload the BOM (bill of materials) and CPL (component placement list) files. These can be found in the same location as the GERBER zip file uploaded earlier, upload these and select "Process BOM & CPL". The next page 

### Operation

It's relatively simple in it's operation. On start-up the RP2040 waits for the AP33772 to check for PD capabilities and negotiate the 9V, then the RP2040 sets itself up and checks it's flash memory to restore any information on the break-in process that was present before losing power. During the wake up process the RP2040 enables the boost converter, starting the motor. The screen displays the amount of actuations it has counted and saves this value to the flash memory every 10 seconds to avoid wearing down the memory write cycles. After 250,000 actuations are counted, the motor is disabled and the screen will prompt you to rotate the switch trays and press the reset (top right) button to continue. This is especially useful considering the off centre implementation. The angle the switches are actuated at isn't too aggressive, so running in off centre at all times was a very tempting idea. The only issue was ensuring each side received an even distribution of actuations, hence the introduction of the load disconnect function. The screen will tell you which rotation of the switch trays you are on, corresponding with the number on the side of the trays.

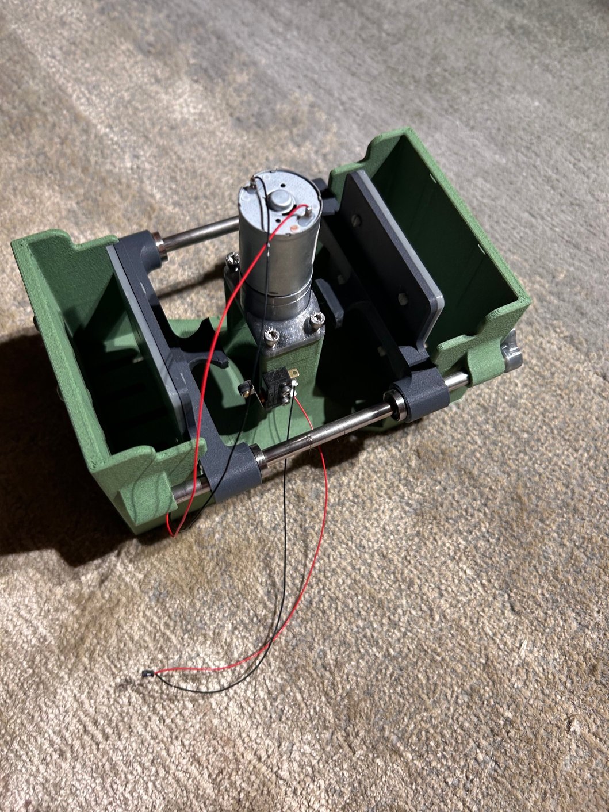
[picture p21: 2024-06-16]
Images/A_Install-Motor-Assembly.jpeg

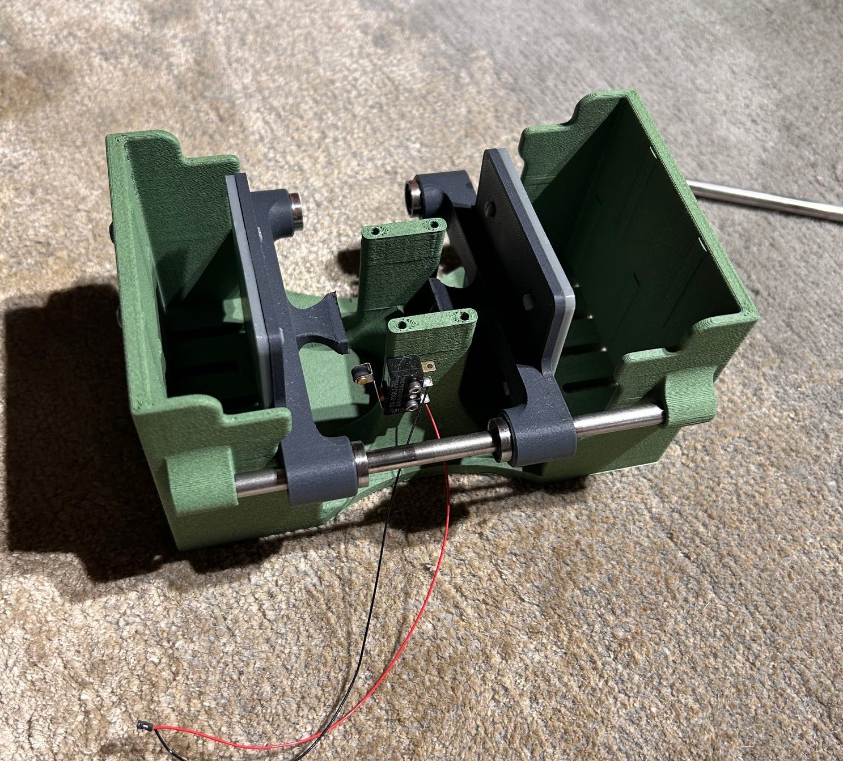
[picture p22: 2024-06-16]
Images/A_Install-Pistons2.jpeg

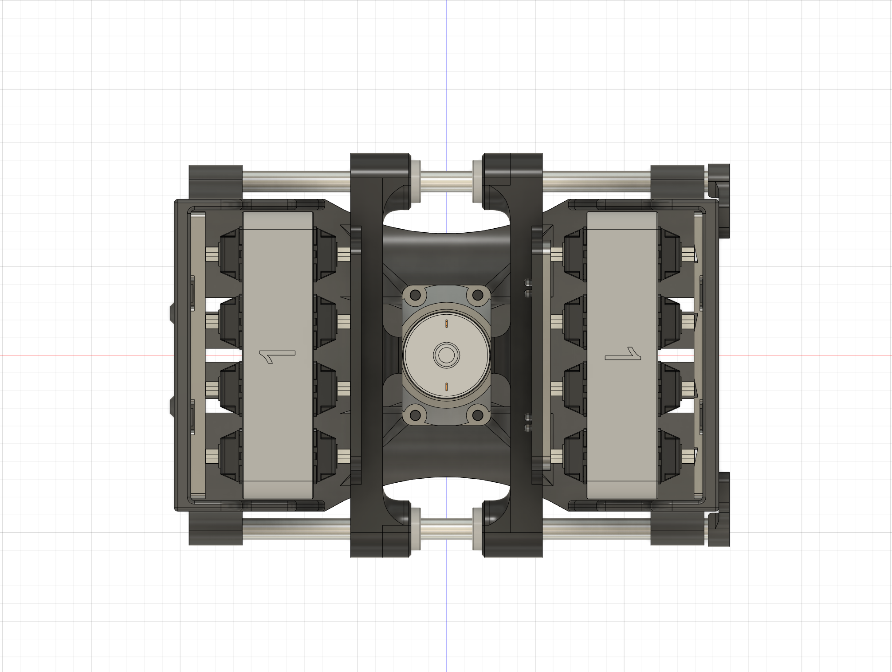
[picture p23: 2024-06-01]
Images/Assembly-Top.PNG

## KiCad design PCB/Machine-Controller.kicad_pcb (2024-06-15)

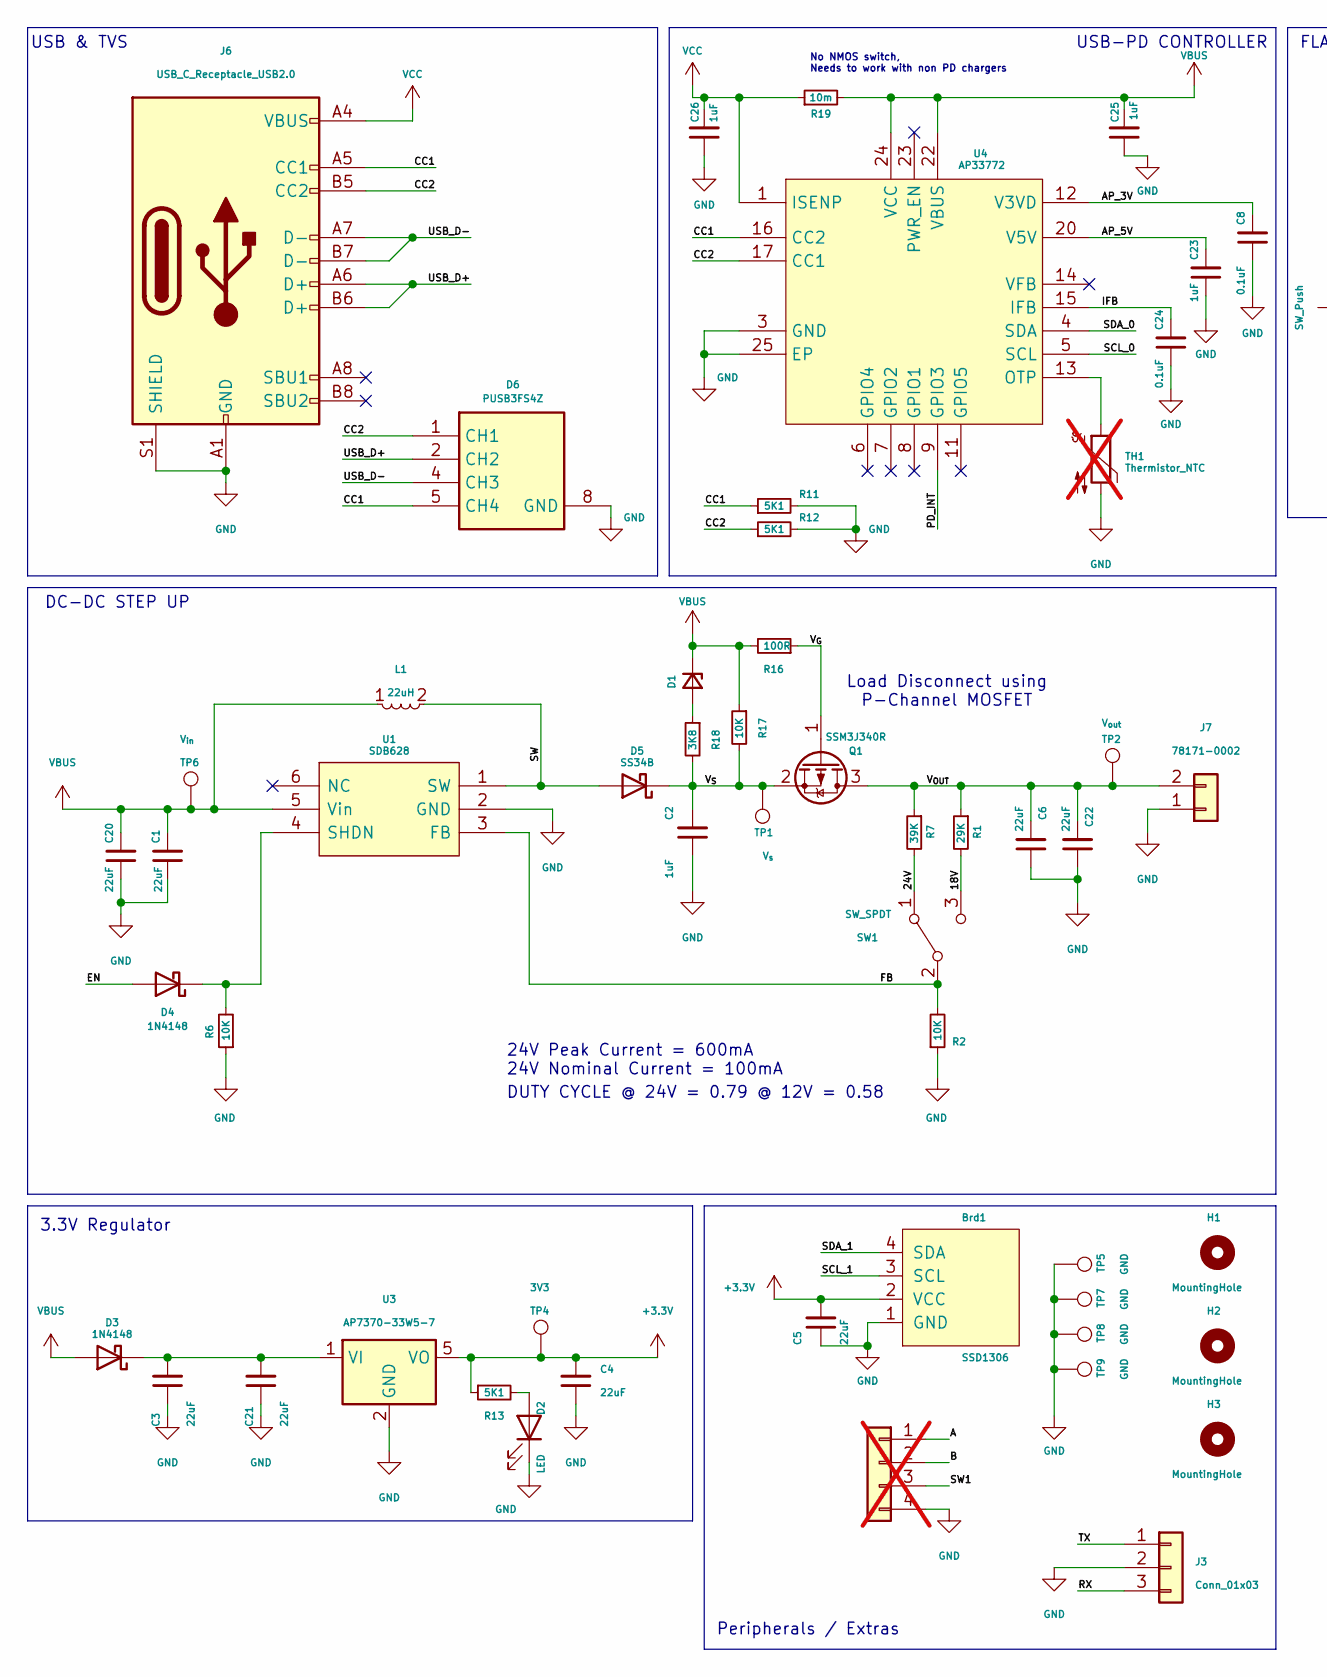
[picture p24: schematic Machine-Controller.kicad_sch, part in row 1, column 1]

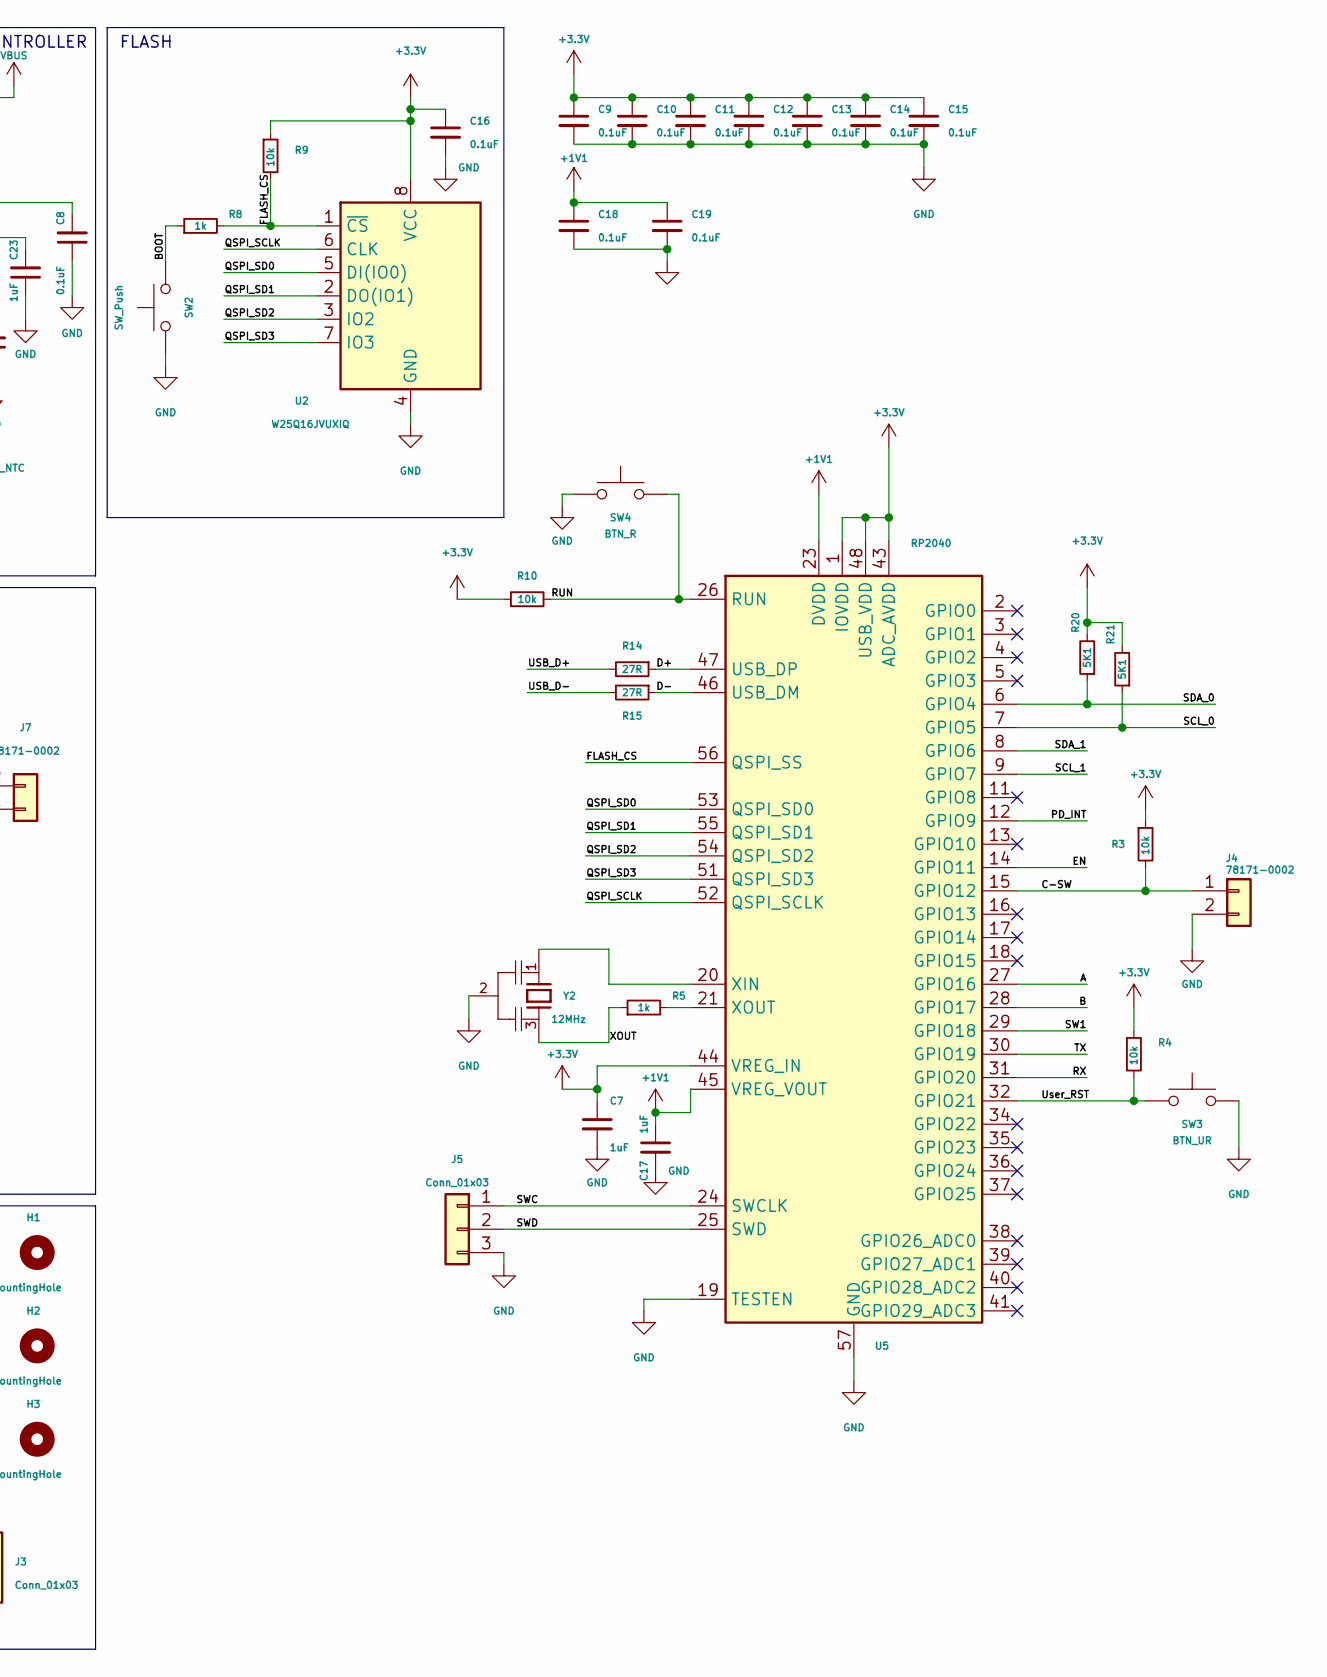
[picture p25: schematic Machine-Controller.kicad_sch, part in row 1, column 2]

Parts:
Brd1: SSD1306; Display_128x64_096_I2C; Manufacturer_Part_Number SSD1306 128x66
C1, C3, C6, C20, C21, C22: 22uF; C_0805_2012Metric
C2: 1uF; C_0805_2012Metric
C4, C5: 22uF; C_0603_1608Metric
C7, C17, C23, C25, C26: 1uF; C_0603_1608Metric
C8, C9, C10, C11, C12, C13, C14, C15, C16, C18, C19, C24: 0.1uF; C_0402_1005Metric
D1: BZX84C22-7-F; SOT-23-3
D2: LED; LED_0603_1608Metric
D3, D4: 1N4148; D_SOD-323F
D5: SS34B; D_SMB
D6: PUSB3FS4Z; DFN2510A-10; Mouser Part Number 771-PUSB3FS4Z
H1, H2, H3: MountingHole; M2_Screw_PTH
J2: Conn_01x05; Molex_Pico-EZmate_78171-0004_1x04-1MP_P1.20mm_Vertical; not fitted
J3: Conn_01x03; PinSocket_1x03_P2.54mm_Vertical
J4, J7: 78171-0002; Molex_Pico-EZmate_78171-0002_1x02; Manufacturer_Part_Number 78171-0002
J5: Conn_01x03; JST_SH_BM03B-SRSS-TB_1x03-1MP_P1.00mm_Vertical
J6: USB_C_Receptacle_USB2.0; USB_C_Receptacle_HRO_TYPE-C-31-M-12; Manufacturer_Part_Number TYPE-C-31-M-12
L1: 22uH; TDK-VLS5045-5x5.3x4.5; Manufacturer_Part_Number 74438356220
Q1: SSM3J340R; SOT-23-3F
R1: 29K; R_0805_2012Metric
R2, R6, R17: 10K; R_0603_1608Metric
R3, R4, R9, R10: 10k; R_0603_1608Metric
R5, R8: 1k; R_0402_1005Metric
R7: 39K; R_0805_2012Metric
R11, R12, R13, R20, R21: 5K1; R_0603_1608Metric
R14, R15: 27R; R_0603_1608Metric
R16: 100R; R_0603_1608Metric
R18: 3K8; R_0603_1608Metric
R19: 10m; R_0603_1608Metric
SW1: SW_SPDT; SW_Slide_1P2T_CK_OS102011MS2Q
SW2: SW_Push; PinHeader_1x02_P2.00mm_Vertical
SW3: BTN_UR; SW_SPST_TL3342; Manufacturer_Part_Number TS-1187A-B-A-B
SW4: BTN_R; SW_SPST_TL3342; Manufacturer_Part_Number TS-1187A-B-A-B
TH1: Thermistor_NTC; C_0402_1005Metric; not fitted
TP1: V_{s}; Keystone_5000-5004_Miniature
TP2: V_{out}; Keystone_5000-5004_Miniature
TP4: 3V3; Keystone_5000-5004_Miniature
TP5, TP7, TP8, TP9: GND; TestPoint_THTPad_1.5x1.5mm_Drill0.7mm
TP6: V_{in}; Keystone_5000-5004_Miniature
U1: SDB628; SOT-23-6; Manufacturer_Part_Number SDB628
U2: W25Q16JVUXIQ; USON-8_2x3x0.6mm; Manufacturer_Part_Number W25Q16JVUXIQ
U3: AP7370-33W5-7; SOT-23-5
U4: AP33772; QFN50P400X400X80-25N-D; Mouser Part Number 621-AP33772DKZ-13
U5: RP2040; RP2040-QFN-56
Y2: 12MHz; OSC_CSTNE12M0G520000R0; PARTREV JGC42-8858A

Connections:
+1V1: C17.1, C18.1, C19.1, U5.23 (DVDD), U5.45 (VREG_VOUT), U5.50 (DVDD)
+3.3V: Brd1.2 (VCC), C4.2, C5.2, C7.1, C9.1, C10.1, C11.1, C12.1, C13.1, C14.1, C15.1, C16.1, R3.1, R4.1, R9.1, R10.1, R13.1, R20.2, R21.2, TP4.1, U2.8 (VCC), U3.5 (VO), U5.1 (IOVDD), U5.10 (IOVDD), U5.22 (IOVDD), U5.33 (IOVDD), U5.42 (IOVDD), U5.43 (ADC_AVDD), U5.44 (VREG_IN), U5.48 (USB_VDD), U5.49 (IOVDD)
/18V: R1.2, SW1.3 (C)
/24V: R7.2, SW1.1 (A)
/A: J2.1, U5.27 (GPIO16)
/AP_3V: C8.2, U4.12 (V3VD)
/AP_5V: C23.2, U4.20 (V5V)
/B: J2.2, U5.28 (GPIO17)
/BOOT: R8.1, SW2.2
/C-SW: J4.1, R3.2, U5.15 (GPIO12)
/CC1: D6.5 (CH4), D6.6 (NC1), J6.A5 (CC1), R11.1, U4.16 (CC2)
/CC2: D6.1 (CH1), D6.10 (NC4), J6.B5 (CC2), R12.1, U4.17 (CC1)
/D+: R14.1, U5.47 (USB_DP)
/D-: R15.1, U5.46 (USB_DM)
/EN: D4.2 (A), U5.14 (GPIO11)
/FB: R2.2, SW1.2 (B), U1.3 (FB)
/FLASH_CS: R8.2, R9.2, U2.1 (~CS), U5.56 (QSPI_SS)
/IFB: C24.2, U4.15 (IFB)
/PD_INT: U4.9 (GPIO3), U5.12 (GPIO9)
/QSPI_SCLK: U2.6 (CLK), U5.52 (QSPI_SCLK)
/QSPI_SD0: U2.5 (DI(IO0)), U5.53 (QSPI_SD0)
/QSPI_SD1: U2.2 (DO(IO1)), U5.55 (QSPI_SD1)
/QSPI_SD2: U2.3 (IO2), U5.54 (QSPI_SD2)
/QSPI_SD3: U2.7 (IO3), U5.51 (QSPI_SD3)
/RUN: R10.2, SW4.2, U5.26 (RUN)
/RX: J3.3, U5.31 (GPIO20)
/SCL_0: R21.1, U4.5 (SCL), U5.7 (GPIO5)
/SCL_1: Brd1.3 (SCL), U5.9 (GPIO7)
/SDA_0: R20.1, U4.4 (SDA), U5.6 (GPIO4)
/SDA_1: Brd1.4 (SDA), U5.8 (GPIO6)
/SW: D5.2 (A), L1.2, U1.1 (SW)
/SW1: J2.3, U5.29 (GPIO18)
/SWC: J5.1, U5.24 (SWCLK)
/SWD: J5.2, U5.25 (SWD)
/TX: J3.1, U5.30 (GPIO19)
/USB_D+: D6.2 (CH2), D6.9 (NC3), J6.A6 (D+), J6.B6 (D+), R14.2
/USB_D-: D6.4 (CH3), D6.7 (NC2), J6.A7 (D-), J6.B7 (D-), R15.2
/User_RST: R4.2, SW3.1, U5.32 (GPIO21)
/V_{G}: Q1.1 (G), R16.1
/V_{OUT}: C6.2, C22.2, J7.2, Q1.3 (D), R1.1, R7.1, TP2.1
/V_{S}: C2.2, D5.1 (K), Q1.2 (S), R17.2, R18.2, TP1.1
/XOUT: R5.1, Y2.3
GND: Brd1.1 (GND), C1.1, C2.1, C3.1, C4.1, C5.1, C6.1, C7.2, C8.1, C9.2, C10.2, C11.2, C12.2, C13.2, C14.2, C15.2, C16.2, C17.2, C18.2, C19.2, C20.1, C21.1, C22.1, C23.1, C24.1, C25.1, C26.1, D2.1 (K), D6.3 (GND), D6.8 (GND), J2.4, J3.2, J4.2, J5.3, J6.A1 (GND), J6.A12 (GND), J6.B1 (GND), J6.B12 (GND), J6.S1 (SHIELD), J7.1, R2.1, R6.1, R11.2, R12.2, SW2.1, SW3.2, SW4.1, TH1.2, TP5.1, TP7.1, TP8.1, TP9.1, U1.2 (GND), U2.4 (GND), U3.2 (GND), U4.3 (GND), U4.25 (EP), U5.19 (TESTEN), U5.57 (GND), Y2.2
unnamed: D1.1 (A), R18.1
unnamed: D2.2 (A), R13.2
unnamed: C3.2, C21.2, D3.1 (K), U3.1 (VI)
unnamed: D4.1 (K), R6.2, U1.4 (SHDN)
unnamed: TH1.1, U4.13 (OTP)
unnamed: U5.20 (XIN), Y2.1
unnamed: R5.2, U5.21 (XOUT)
VBUS: C1.2, C20.2, C25.2, D1.2 (NC), D1.3 (K), D3.2 (A), L1.1, R16.2, R17.1, R19.2, TP6.1, U1.5 (Vin), U4.22 (VBUS), U4.24 (VCC)
VCC: C26.2, J6.A4 (VBUS), J6.A9 (VBUS), J6.B4 (VBUS), J6.B9 (VBUS), R19.1, U4.1 (ISENP)

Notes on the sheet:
Peripherals / Extras
3.3V Regulator
No NMOS switch, Needs to work with non PD chargers
DUTY CYCLE @ 24V = 0.79 @ 12V = 0.58
USB & TVS
Load Disconnect using P-Channel MOSFET
DC-DC STEP UP
USB-PD CONTROLLER
FLASH
24V Peak Current = 600mA 24V Nominal Current = 100mA

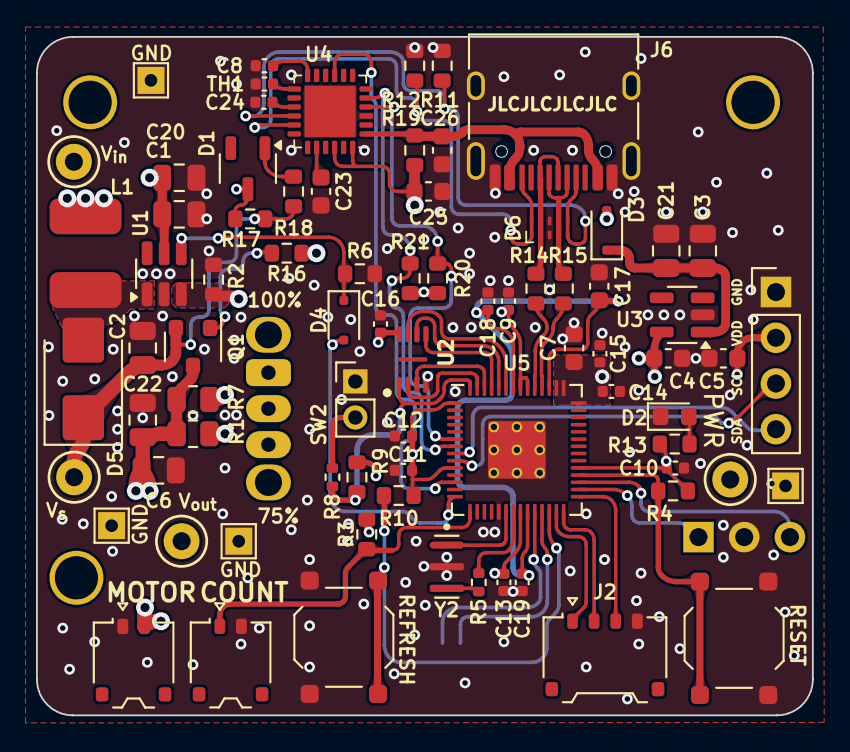
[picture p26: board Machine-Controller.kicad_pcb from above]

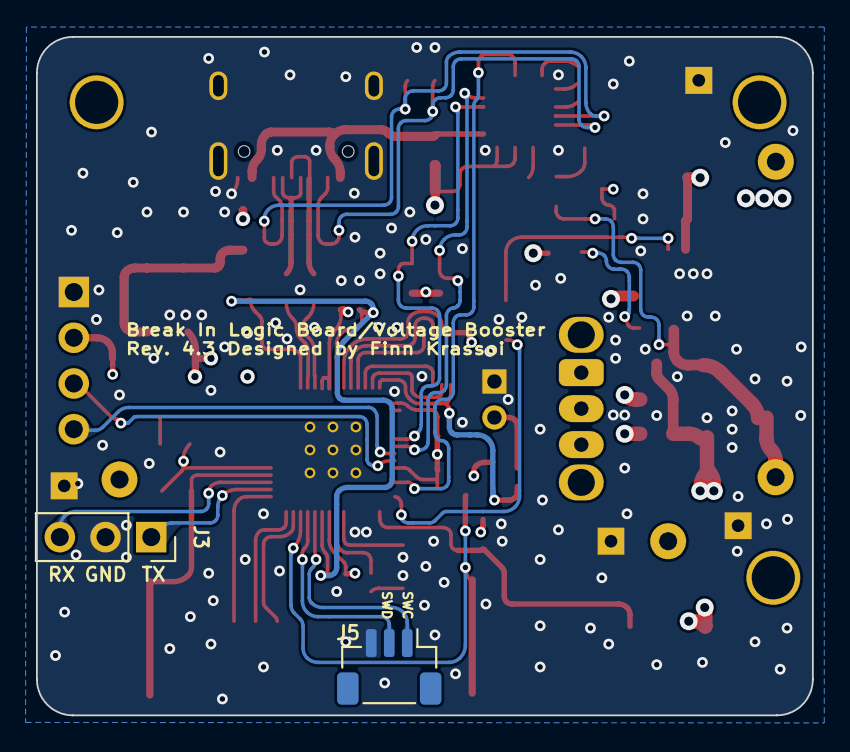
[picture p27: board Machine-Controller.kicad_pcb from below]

Board: 4 copper layers, 43.1 x 37.7 mm, 84 parts (2 on the bottom side), 52 nets.

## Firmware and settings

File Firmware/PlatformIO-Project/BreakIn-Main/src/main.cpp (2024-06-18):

#include <Arduino.h>
#include <Wire.h>
#include <LittleFS.h>
#include <Adafruit_GFX.h>
#include <Adafruit_SSD1306.h>
#include <AP33772.h>
#include <Bounce2.h>

#define SCREEN_WIDTH 128
#define SCREEN_HEIGHT 64

#define SCREEN_ADDRESS 0x3C

#define SWITCH_PIN 12
#define RESET_PIN 21
#define CONTROL_PIN 11
#define COUNT_FILE "/counter.txt"
#define ROTATION_FILE "/rotation.txt"

void initDisplay();
void saveCountToFile();
void saveRotationToFile();
void updateDisplay();
void resetCount();


int counter = 0;
int rotation = 0;
bool countReset = false;
unsigned long lastWrite = 0;

AP33772 usbpd;

enum resetBtnState {
  NO_PRESS = 0,
  SHORT_PRESS,
  LONG_PRESS
};

Adafruit_SSD1306 display(SCREEN_WIDTH, SCREEN_HEIGHT, &Wire1);

bool button_was_pressed() {
  static bool last_state = HIGH;
  bool current_state = digitalRead(SWITCH_PIN);

  if (!current_state && last_state) {
    delay(10);
    current_state = digitalRead(SWITCH_PIN);
    if (!current_state) {
      last_state = current_state;
      return true;
    }
  }
  last_state = current_state;
  return false;
}

// Only returns true if the button is pressed for under 1 second
resetBtnState checkButton() {
  static bool lastState = HIGH;
  static unsigned long pressTime = 0;
  //static unsigned long debounceTime = 0; //No delay debounce

  bool currentState = digitalRead(RESET_PIN);

  // Check if pressed
  if (currentState != lastState) {
    if (currentState == LOW) {

      pressTime = millis();
    } else {
        unsigned long pressDuration = millis() - pressTime;
        lastState = currentState;

        if (pressDuration >= 1000) {
          return LONG_PRESS;
        } else {
          return SHORT_PRESS;
      }
    }
  }

  lastState = currentState;
  return NO_PRESS;
}


void setup() {
  // Setup debug output
  Serial2.setTX(24);
  Serial2.setRX(25);
  Serial2.begin(115200);

  // Setup SSD1306 output
  Wire1.setSDA(6);
  Wire1.setSCL(7);
  Wire1.begin();

  // Setup USB-C PD interface output
  Wire.setSDA(4);
  Wire.setSCL(5);
  Wire.begin();
  
  // Delay is necessary for processor to acquire PDOs
  delay(1000);

  initDisplay();

  // Negotiate 27W (9V 3A) from PD charger
  usbpd.begin();
  usbpd.setVoltage(9000);
  usbpd.setMaxCurrent(3000);

  Serial2.println("Setting up");

  // Setup GPIO roles
  pinMode(SWITCH_PIN, INPUT_PULLUP);
  pinMode(RESET_PIN, INPUT_PULLUP);
  pinMode(CONTROL_PIN, OUTPUT_12MA);
  
  digitalWrite(CONTROL_PIN, HIGH);

  Serial2.println("motor on, setup complete");

  // Initialise LittleFS, look for file & set counter value. If file not found, create file and set count value to 0.
  if (!LittleFS.begin()) {
    Serial2.println("LittleFS failed to start up");
  }

  File countFile = LittleFS.open(COUNT_FILE, "r");
  if (countFile) {
    counter = countFile.parseInt();
    countFile.close();
  } else {
    Serial2.println("Failed to read value from file, set to default value of 0");
    counter = 0;
    saveCountToFile();
  }

  File rotationFile = LittleFS.open(ROTATION_FILE, "r");
  if (rotationFile) {
    rotation = rotationFile.parseInt();
    rotationFile.close();
  } else {
    rotation = 1;
    saveRotationToFile();
  }

  updateDisplay();
}

void loop() {

  // Increment value of counter as switch is pressed. Save value of count every 10 seconds.
  if (button_was_pressed()) {
    counter++;
    if(millis() - lastWrite > 10000) {
      saveCountToFile();
      lastWrite = millis();
    }
    updateDisplay();
  }
  
  resetBtnState buttonState = checkButton();

  if (counter >= 250000) {
    digitalWrite(CONTROL_PIN, LOW);
    display.clearDisplay();
    display.setTextSize(2);
    display.setCursor(28,0);
    display.print(F("ROTATE"));
    display.setCursor(16,18);
    display.print(F("SWITCHES"));
    display.setTextSize(1);
    display.setCursor(52,36);
    display.print(F("THEN"));
    display.setCursor(49,46);
    display.print(F("RESET"));
    display.display();
    if (buttonState == resetBtnState::SHORT_PRESS) {
      rotation++;
      if (rotation <= 4) {
        digitalWrite(CONTROL_PIN, HIGH);
        saveRotationToFile();
      } else {
        rotation = 1;
        saveRotationToFile();
      }
    }
  }


  // Multifunction reset/power button
  switch (buttonState) {
    case LONG_PRESS: {

      int controlState = digitalRead(CONTROL_PIN);

      if (controlState == LOW) {
        digitalWrite(CONTROL_PIN, HIGH);
      } else {
        digitalWrite(CONTROL_PIN, LOW);
      }
      break;
    }
    case SHORT_PRESS:
      resetCount();
  }
}

void initDisplay() {
  if (!display.begin(SSD1306_SWITCHCAPVCC, SCREEN_ADDRESS)){
    Serial2.println("SSD1306 allocation failed");
  }
  // Clear buffer
  display.clearDisplay();
  display.setTextSize(1);
  display.setTextColor(SSD1306_WHITE);
}

void updateDisplay() {
  display.clearDisplay();
  display.setCursor(0,0);
  display.print(F("Actuations"));
  display.setCursor(0,10);
  display.setTextSize(2);
  display.println(counter);
  display.setCursor(0,28);
  display.setTextSize(1);
  display.print(F("Rotation"));
  display.setCursor(0,38);
  display.println(rotation);
  display.display();
}

void saveCountToFile() {
  File countFile = LittleFS.open(COUNT_FILE, "w");
  if (countFile) {
    countFile.print(counter);
    countFile.close();
    Serial2.println("Saved Count Value to File");
  } else {
    Serial2.println("Failed to Save Count to File");
  }
}

void saveRotationToFile() {
  File rotationFile = LittleFS.open(ROTATION_FILE, "w");
  if (rotationFile) {
    rotationFile.print(rotation);
    rotationFile.close();
  } else {
    Serial2.println("Failed to save rotation to file");
  }
}

void resetCount() {
  display.clearDisplay();
  display.setTextSize(1);
  display.setCursor(0, 0);
  display.print(F("RESET ACTUATIONS"));
  display.display();
  delay(1000);

  Serial2.println("Actuations set to null");
  //Overwrite saved value
  counter = 0;
  saveCountToFile();
  updateDisplay();
}

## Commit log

2024-06-01 add 3D models
    [4x4-Switch-Tray.step, Back-Plate.step, Machine-Controller.kicad_sch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]
2024-06-05 BoM and Docs
    [BOM-Machine-Controller.csv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]
2024-06-16 calibration stl
    [Piston-Calibration.stl]
2024-06-17 Fixes malformed links in BOM
    added missing `https://` prefix that was causing AE links to 404 when viewing on github as markdown.
2024-06-18 Fixed Bug in FW
    [main.cpp]
